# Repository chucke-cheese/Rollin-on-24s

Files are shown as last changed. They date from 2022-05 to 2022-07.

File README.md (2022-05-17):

The purpose of this project is to take a coin operated game such as Bob's Space Racers' Rollin' On 24's, and modify it so that the guest no longer has to reach up to the top of the game where the coin mech is to play the game. The guest will be able to play the game from a button lower down on the game, so that shorter guests can comfortably play the game, similar to how Andamiro's Spongebob Pineapple Arcade plays.

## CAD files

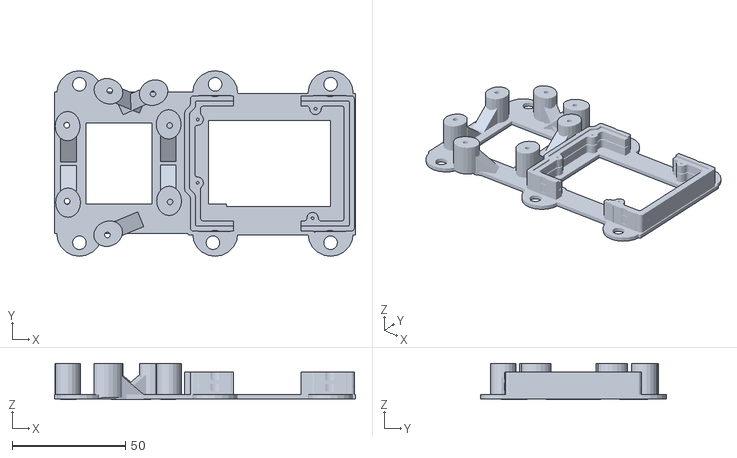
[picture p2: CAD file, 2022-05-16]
Token game modifier base v2.stl
133.0 x 82.0 x 16.0

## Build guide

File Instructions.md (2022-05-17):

The purpose of this project is to take a coin operated game such as UNIS's Rollin' On 24's, and modify it so that the guest no longer has to reach up to the top of the game where the coin mech is to play the game. The guest will be able to play the game from a button on the game, so that shorter guests can comfortably play the game.

If the game to be modified is in an establishment that no longer uses tokens, the machine may be modified already to use a coin dispenser system, such as Speedy's One Stop Shop's Coin Hopper Mounting System (see ref 1). This system includes everything that one would need to make a coin operated game able to use a card system (except the card system.) The brains behind this system is a hopper control board that dispences the coin to the guest when it receives a credit-in signal. In the case of Speedy's control board, the credit input line is red. This line and any one of the six ground lines is the focus of this project.

The circuit needed for this project is named "Modified Hopper Wiring.pdf" Keep in mind that for this to work, there must be enough room next to the coin chute to place a hopper so that the hopper can dispense the coin directly into the game (see Example.jpg). Games such as UNIS's Rollin' on 24's or UNIS's Basket Fortune have enough room next to the coin chute.

The Items needed for this project are:
1.) Arduino (code provided)
2.) Arduino IDE (required to upload Arduino code to Arduino)
3.) 2 channel relay board
4.) light-up button
5.) Base for arduino and 2 channel relay board (stl and gcode files provided) (Optional)

Basic Version of Getting started in Arduino (see ref 2A)
The Arduino Uno is the basic beginners board (as well as the most common.) It has 14 digital input/outputs, 6 analog inputs, and a 16MHz clock. This allows it to interface with a variety of sensors and applications. The Uno operates at 5V, and can be powered via the USB port, or it can take an input voltage of 6-20V (7-12 recommended) on the Vin pin. It can also be powered through the barrel jack at 12V.The 5V pin can supply 1A max for powering external sensors and outputs, if more then that is required you need an external power supply. If you try to draw more then 1A, the board will be damaged. The Arduino Uno measures 2.7" by 2.1". After installing the Arduino IDE, you can begin programming the Arduino. After creating the code, or opening existing code, go to "Tools" - "Board", and choose which board you are using. Then, go to "Tools" - "Port" and choose the port that corresponds to your Arduino. Optimally, if you have only one Arduino plugged in, the port shown in the menu should be the correct one. More information and troubleshooting options can be found in ref 2B if you are having issues getting everything working. Reference 2C is the Arduino list of boards and products.

The 2-channel relay board is different from just 2 relays, because 2 relays would draw all their current from the digital pins of the Arduino, possibly damaging it. The 2-channel relay board adraws its power from either the 5v pin of the Arduino, or an external 5v power supply, and takes only its signal from the digital pins.

The subroutine flow chart for the hopper control board is listed in the patent information (see ref 3). This does not change in this project. Normally, when the guest taps or swipes their card, the card system sends a credit-in signal to the hopper control board to tell it to dispense a coin. This project interupts that signal. Instead, the signal goes to an arduino, which counts the credit-in as a +1. The Arduino also engages a relay that allows the guest to press a button that sends the credit-in signal to the hopper control board. The light in the button also lights up, from another relay. When the hopper dispenses the coin into the game, the coin triggers a coin switch that tells the game that a coin has been inserted. This switch also tells the Arduino the same thing, causing the Arduino to count a -1. Once the count in the Arduino reaches 0, both relays switch off, turning off the light in the button, and disengaging the button. The counter in the Arduino allows for multi-credit input, retaining the credit until played, or the game is turned off.

The coinmech will have to be removed for this to work. The hole will have to be covered by something. ICE Games sells a "Marquee Ball Catch" (RB3042) that works well for this, as it is a 1/8" thick sheet of black plastic.

For reference, the card system has an Interface Board with these connections:
All black wires are common ground, and all red wires are common 12VDC. This board contains 2 relays. One is connected to J3, and the other is a feature that enables the ticket mech shound the reader be unplugged.
J1 connects in between the Ticket mech and the game. It is a good idea to power the card reader system from an external power supply, rather than taking power from the game's power supply. This can be done using a 12VDC power supply plugged into the on board barrel jack (J7), or by cutting the red wire coming from J1 and wiring the board side of the wire to a 12VDC power supply. There are six wires coming from this connector. Pin 1 is white and black, and goes to the game enable. Pin 2 s common ground. Pin 3 is common 12VDC. Pin 4 is blue and black, and goes to game notch. Pin 5 is white, and goes to the ticket mech enable (which is normally disconnected inside the interface board, but is enabled if the reader is disconnected.) Pin 6 is blue and connects to the mech notch.
J2 connects to the coin signal from game via the brown wire. The red and black wires are generally not used.
J3's brown wire is the coin enable, or in the case of this circuit, connects to the arduino to tell the arduino to count up 1 credit. Connect the black wire to a ground pin of the Arduino.
J5 connects to the reader via a ribbin cable.
J7 connects to an optional external 12VDC power supply.

References
1A.)http://www.alphaomegasales.com/token-hopper-mounting-system-quick-coin-games-speedys-one-stop/
1B.)http://www.sosrepairservice.com/downloads/Speedys_Coin_Hopper_Brochure.pdf#toolbar=0
1C.)http://www.sosrepairservice.com/coinhopper.asp
2A.)https://www.instructables.com/Getting-Started-with-Arduino-3/
2B.)https://www.arduino.cc/en/Guide/HomePage
2C.)www.arduino.cc/en/Main/Products
3.)https://patft.uspto.gov/netahtml/PTO/index.html Patent number US 10,223,867 B2

Interesting github, unrelated to this project: https://github.com/telarium/chuckECheese_animatronic

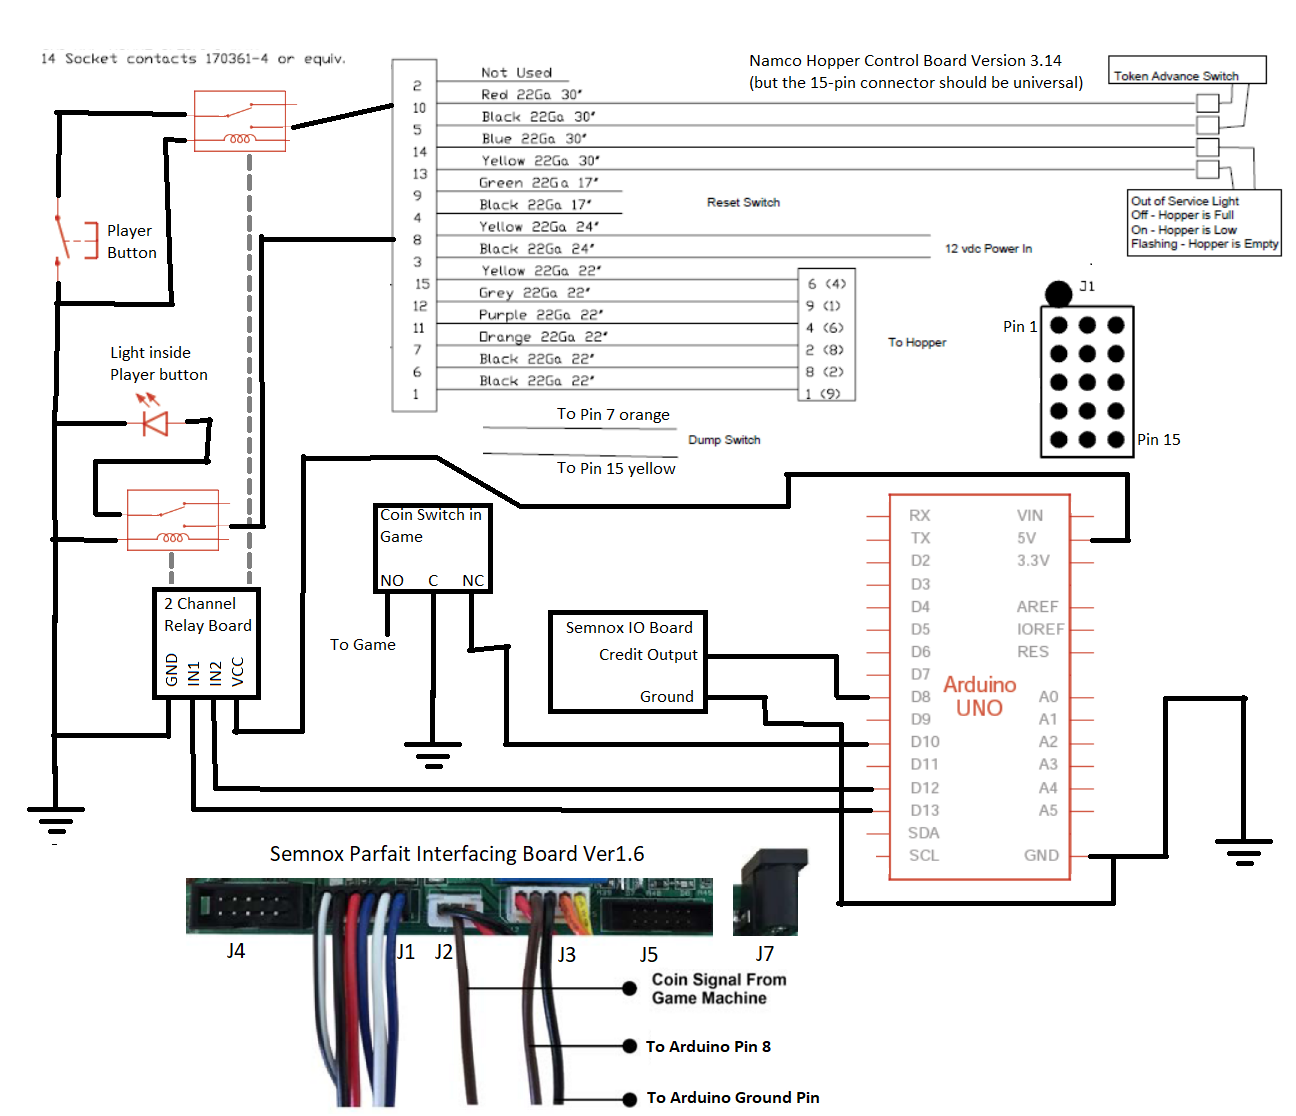
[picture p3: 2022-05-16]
Modified hopper wiring.png

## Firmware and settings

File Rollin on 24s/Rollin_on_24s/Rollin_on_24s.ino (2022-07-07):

//HIGH is ON on the four channel Relay Board
//LOW is OFF on the four channel Relay Board
//HIGH is OFF on the two channel Relay Board
//LOW is ON on the two channel Relay Board

const int light = 13;      // the number of the button light
const int hopper =  12;      // the number of the hopper
const int coinMech = 3;     // the number of the coin mech pin
const int creditPin = 8;     // the number of the IO Board credit pin

// variables will change:
int creditState = 0;         // variable for reading the pushbutton status
int coinState = 0;
int count = 0;              // credit counter

void setup() {
  // initialize the LED pin as an output:
  pinMode(hopper, OUTPUT);
  pinMode(light, OUTPUT);
  // initialize the pushbutton pin as an input:
  pinMode(creditPin, INPUT_PULLUP);
  pinMode(coinMech, INPUT_PULLUP);
  digitalWrite(hopper, LOW);
  digitalWrite(light, LOW);
  //Serial.begin(9600);
}

void loop() {
  creditState = digitalRead(creditPin);
  // check if the pushbutton is pressed. If it is, the buttonState is HIGH:
  if (creditState == LOW) {
    count = ++count;
    digitalWrite(hopper, HIGH);
    digitalWrite(light, HIGH);
    delay(1000);
  }
  coinState = digitalRead(coinMech);
  if (coinState == LOW){ //change to HIGH in the game
    if (count > 0){
      count = count - 1;
    }
    if (count == 0){
      digitalWrite(hopper, LOW);
      digitalWrite(light, LOW);
    }
    //Serial.println(count);
    delay(250);
  }
}
